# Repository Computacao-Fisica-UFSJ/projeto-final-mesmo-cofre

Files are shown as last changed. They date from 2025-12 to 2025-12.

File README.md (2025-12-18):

# 🐾 Projeto Yummy

- **Autores:** Ester Maria e Mateus Brito
- **Baseado em:** [Automatic Arduino Powered Pet Feeder](https://www.instructables.com/Automatic-Arduino-Powered-Pet-Feeder/)
- **Data:** 2025-12-17

---

## Sumário
- [Contextualização](#contextualização)
- [Guia do Usuário](#guia-do-usuario)
- [Código e Bibliotecas](#código-e-bibliotecas)
- [Lista de Materiais](#lista-de-materiais)
- [Diagrama da Montagem (Fritzing)](#diagrama-da-montagem-fritzing)
- [Explicação do Diagrama](#explicação-do-diagrama)
- [Foto do Projeto Montado](#foto-do-projeto-montado)
- [Vídeo do Projeto em Funcionamento](#vídeo-do-projeto-em-funcionamento)
- [Problemas Encontrados](#problemas-encontrados)
- [Evolução do Projeto](#evolução-do-projeto)
- [Referências](#referências)
- [Créditos](#créditos)

---

## Contextualização
O **Projeto Yummy** consiste no desenvolvimento de um alimentador automático de pets, utilizando a plataforma Arduino, com foco em automação, controle de quantidade de ração e interação do usuário via interface web.

A motivação do projeto surge da necessidade de garantir que animais de estimação recebam a quantidade correta de alimento, mesmo na ausência do dono, evitando tanto a subalimentação quanto o excesso de ração. Para isso, o sistema combina atuadores mecânicos, sensor de peso (balança) e conectividade Wi-Fi, permitindo um controle mais preciso e automatizado do processo.

Diferentemente de alimentadores baseados apenas em tempo, o Yummy utiliza uma balança calibrada para medir a quantidade real de ração servida. Dessa forma, o processo de liberação só é finalizado quando o peso configurado pelo usuário é atingido, aumentando a confiabilidade do sistema.

---

## Guia do Usuário
Essa seção descreve como o usuário interage com o alimentador automático por meio do navegador.

### Inicialização do Sistema
- Conecte o Arduíno à fonte de alimentação.
- Aguarde alguns segundos para que o módulo Wi-fi inicializa corretamente.

### Acesso à Interface Web
- O dispositivo deve estar conectado à mesma rede configurada no código .ino (por padrão, o código está conectado à rede da UFSJ).
- Abra um navegador de internet
- Digite o endereço "172.18.191.210" na barra de navegação.
- Ao acessar o endereço, a página de controle do alimentador será exibida.

### Configuração da Quantidade de Ração
- Na interface web, o usuário pode configurar a quantidade de ração desejada, em quilogramas.
- O valor padrão configurado no sistema é 0.06 kg.

### Servir a Ração
- Após definida a quantidade desejada, pressione o botão "Iniciar" na interface.
- O servo agitador começa a movimentar a reção no reservatório.
- Em seguida, o motor responsável pela liberação da ração é acionado.
- A ração é liberada gradualmente.
- A balança monitora o peso em tempo real.
- O sistema interrompe automaticamente a liberação quando o peso configurado é atingido.

### Finalização do Processo
- Ao atingir o peso desejado os motores são desligados e o processo de alimentação é encerrado.
- O sistema fica pronto para uma nova configuração ou novo acionamento.

---

## Códigos e Bibliotecas

### Código principal utilizado
Arquivo principal: 'codigo.ino'

### Bibliotecas (não-padrão)
- **HX711** (`HX711.h`) — *Bogdan Necula*  
  - Via Library Manager: buscar por `HX711`  

- **Servo** — geralmente já disponível na IDE do Arduino (padrão).

### Observações sobre compilação
- Plataforma alvo: **Arduino Uno**
- Antes de compilar, verifique se a biblioteca `HX711` está instalada; caso contrário, instale via **Sketch → Include Library → Manage Libraries**.

---

## Materiais

### 🔌 Componentes 
- **1x** Servo motor (utilizado no projeto: SG90)
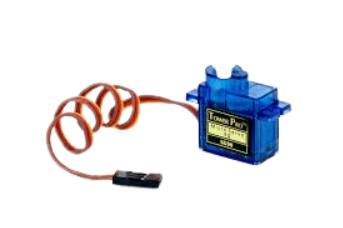
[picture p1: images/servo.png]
Servo Motor
  
- **1x** Micro Motor DC N20 
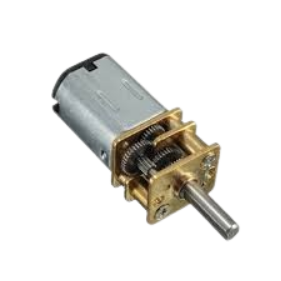
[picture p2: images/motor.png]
Micro Motor
  
- **1x** Peça impressa em 3D para movimentação da ração
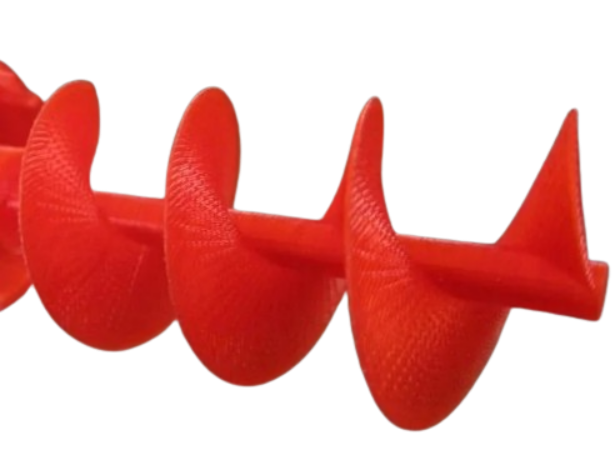
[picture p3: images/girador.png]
Rosca

- **1x** Peça impressa em 3D para agitar a ração
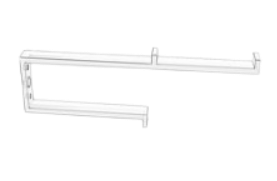
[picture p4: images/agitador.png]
Agitador

- **1x** Tubo de PVC em T de **1 ½"**  
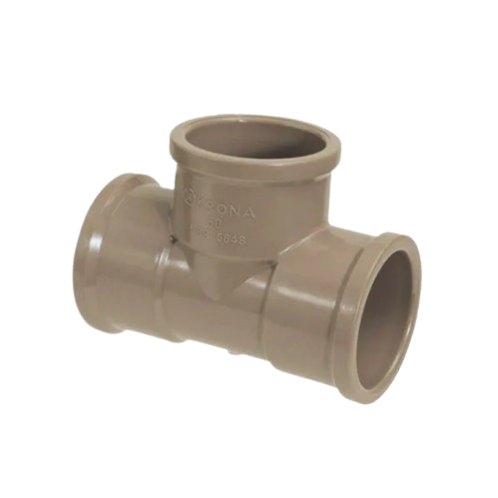
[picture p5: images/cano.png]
Tubo PVC

- **1x** Arduino Mega  
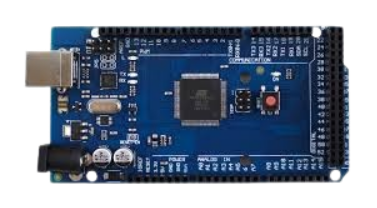
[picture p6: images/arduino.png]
Arduíno Mega

- **1x** Módulo Wi-Fi ESP8266
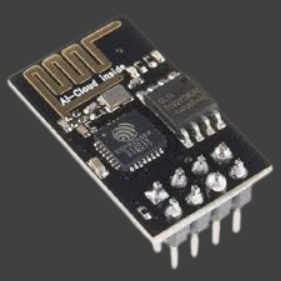
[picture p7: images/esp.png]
Módulo Wi-fi

- **1x** Placa HX711
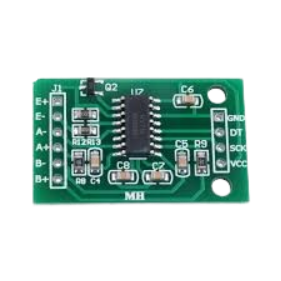
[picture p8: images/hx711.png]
HX711

- **1x** Módulo Ponte H
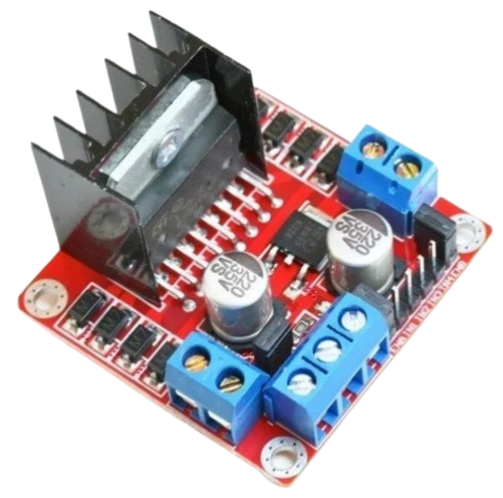
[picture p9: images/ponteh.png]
Ponte H

- **1x** Reservatório de ração 
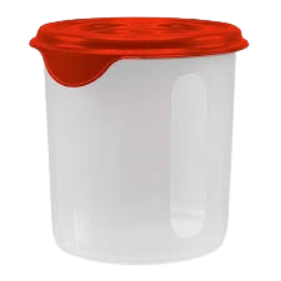
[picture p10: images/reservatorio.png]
Reservatório

- **1x** Caixa de montagem  
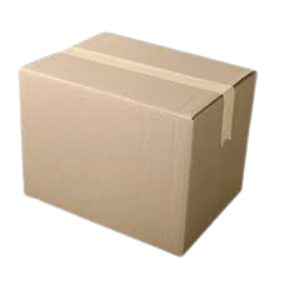
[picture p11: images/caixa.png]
Caixa

- **1x** Balança (Seu sensor de peso foi utilizado)
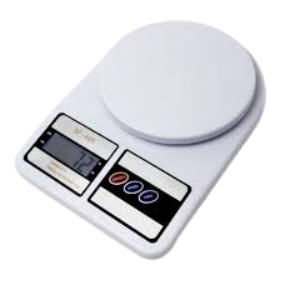
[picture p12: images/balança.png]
Balança

- **1x** Impressora 3D  

---

## Diagrama da Montagem (Fritzing)

- Arquivo Fritzing do projeto: `fritzing/fritzing.fzz`  
- Os componentes que foram importados separadamente se encontram na pasta "fritzing".

---

## Explicação do Diagrama

1. **Arduíno Mega**  
   - **Função**: unidade central de controle do projeto. É responsável por processar os dados da balança, receber comandos da interface web e controlar os motores.
   - **Conexões**: 
      - Alimentação via USB

2. **Servo motor (Agitador de ração)**  
   - **Função**: movimenta a ração dentro do reservatório, evitando que ela fique presa antes de ser liberada.
   - **Conexões**: 
      - Sinal: pino digital
      - VCC: 5V
      - GND: GND

3. **Motor DC (Liberação da ração)**  
   - **Função**: aciona o mecanismo responsável por liberar a ração pelo tubo de PVC.
   - **Conexões**: 
      - Terminais do motor conectados à ponte H

4. **Célula de Carga (Balança)**  
   - **Função**: mede o peso da ração liberada, permitindo que o sistema interrompa o processo ao atingir o valor configurado.
   - **Conexões**: 
      - Fios da célula conectados ao módulo HX711 (E+, E−, A+, A−)

5. **Módulo HX711**  
   - **Função**: amplifica e converte o sinal analógico da célula de carga em dados digitais compreensíveis pelo Arduino.
   - **Conexões**: 
      - DT (Data): pino digital do Arduino
      - SCK: pino digital do arduíno
      - VCC: 5V
      - GND: GND
      - Entradas conectadas à célula de carga

6. **Módulo Wi-Fi (ESP8266)**  
   - **Função**: permite a comunicação do Arduino com a rede Wi-Fi, possibilitando o controle do alimentador via navegador.
   - **Conexões**: 
      - TX: RX do arduíno
      - RX: TX do arduíno
      - VCC: 5V
      - GND: GND

7. **Fonte de Alimentação Externa**  
   - **Função**: fornece energia suficiente para os motores e servos, evitando sobrecarga no Arduino.

---

## Foto do Projeto Montado

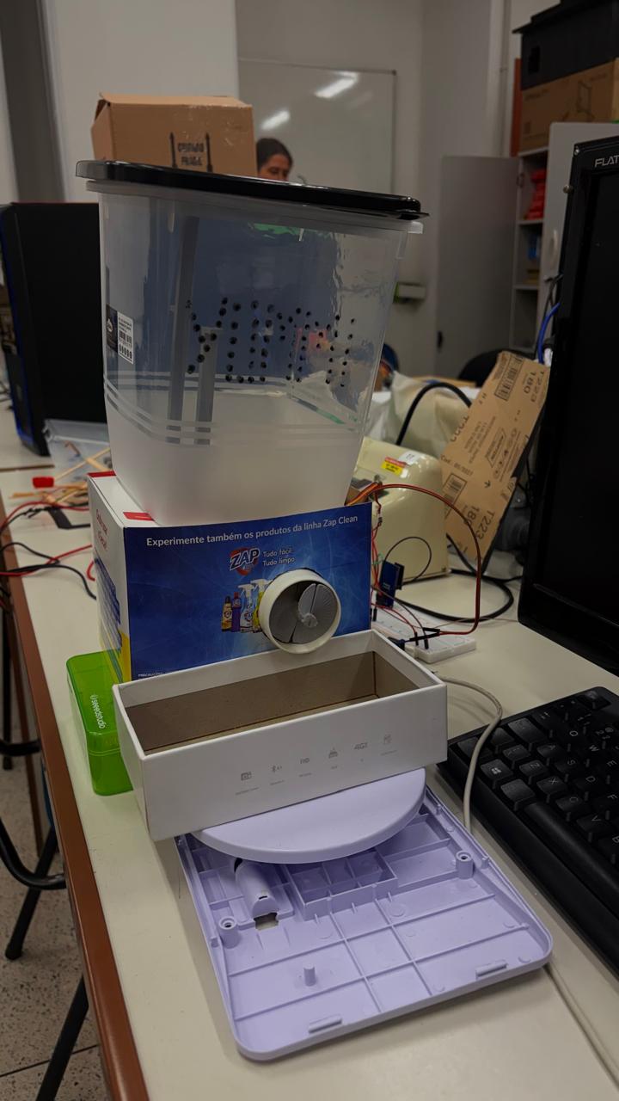
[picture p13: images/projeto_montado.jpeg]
Foto do projeto montado


---

## Vídeo do Projeto em Funcionamento
 
Link direto do vídeo: `https://drive.google.com/file/d/1mnle7g3bbe9a2HnBpE-G1RTfhmxTSZ-H/view?usp=sharing`

---

## Problemas Encontrados no Processo de Montagem

- **Encaixe da rosca no cano PVC:** dificuldade ao fazer o encaixe perfeito da rosca no cano PVC. A conexão da rosca impressa 3d com o motor, e seu encaixe dentro do cano não funcionou bem, ela não rodava sempre com perfeição. Além disso, a fixação do motor foi uma tarefa difícil.
- **Alimentação:** devido à quantidade de componentes do projeto, somente a alimentação do arduíno não foi suficiente.
- **Balança:** realizar a abertura da balança, a calibração da célula de carga e conexão dos fios foi um pouco complicado.
- Em geral, enfrentamos mais dificuldades na parte física do projeto.

---

## Evolução do Projeto

### Etapas realizadas até a aula do dia 19/11:
- Abertura da balança: tentamos entender como a informação é passada pelos componentes da balança e vimos que seria necessário o uso de um módulo conversor para o sensor de peso (HX711).
- Solda dos fios que saem do sensor de peso da balança na placa HX711, e dos fios que saem da mesma placa para serem enviados para a placa Arduíno.
- Com a conexão do sensor de peso ao arduíno, realizamos a calibração da balança com um código.
- Conexão do servo ao projeto: esse servo controlará o agitador de ração. Produzimos um código inicial, o qual aguarda o sinal de botão para agitar a ração, até que um certo peso na balança é atingido. 

### Aula 25/11:
- Análise de motores possíveis para controlar a rosca que libera a ração. Escolhemos o Micro Motor DC N20 e tentamos conectá-lo à uma ponte H para dividir a alimentação. Contudo, tivemos problema com a fonte que utilizamos e resolvemos conectar o motor diretamente ao arduíno. Incluímos essa parte no código, ativando o motor depois que o servo do agitador para, até que o peso seja atingido.

### Aula 26/11:
- Iniciamos a lógica do Wi-Fi, entendendo o funcionamento do módulo ESP8266. Utilizamos um código teste para testarmos o módulo.

### Aula 03/12:
- Unimos o código da lógica do projeto com o código teste do Wi-Fi. Criamos funções com lógica de máquina de estado para o funcionamento do projeto. Começamos o html para o cliente realizar as requisições pela web. Em geral, está funcionando bem. Alguns problemas surgiram no meio do caminho e precisam ser solucionados.

### Aula 09/12:
- Começamos a montar a parte estrutural do projeto. Conectar os componentes, parafusar itens, etc.

### Aula 10/12:
- Tivemos problema com a peça que serve a ração e sua conexão com o motor. O motor não estava estruturalmente estável, o que fazia com que a peça travasse dentro do cano PVC. Passamos o dia tentando solucionar este problema.

### "Aula" 15/12:
- Com o problema da peça que serve a ração inicialmente solucionado, resolvemos problemas com o código, como html para requisição e configuração da tara da balança. Além disso, fizemos as atualizações necessárias no Fritizing do projeto. Ao iniciarmos a montagem do projeto, vimos que a energia fornecida pelo arduíno não seria suficiente, tendo em vista que o motor não estava funcionando. Com isso, foi necessário utilizar fontes de energia externas, como point H.

### "Aula" 15/12:
- Com os problemas estruturais e de software resolvidos, partimos para a montagem final do projeto.
---

## Referências

- Automatic Arduino Powered Pet Feeder: https://www.instructables.com/Automatic-Arduino-Powered-Pet-Feeder/

---

## Créditos

- Arthur Carvalho: ajuda na implementação do Wi-Fi
- Davi Greco: ajuda na solda de alguns componentes
- Milene: ajuda no mental e na parte estrutural

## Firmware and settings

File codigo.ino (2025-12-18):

// INCLUSÃO DE BIBLIOTECAS
#include <HX711.h>
#include <Servo.h>

// DEFINIÇÕES DE PINOS
#define pinDT  2
#define pinSCK  3
#define pinMotor1 8
#define pinMotor2 9
#define DEBUG true

int estado = 0;
int pos = 0;
float pesoDesejado = 0.06;

// INSTANCIANDO OBJETOS
HX711 scale;

// DECLARAÇÃO DE VARIÁVEIS
float medida = 0;
Servo agitadorServo;

void setup() {
  Serial.begin(57600);
  Serial1.begin(115200); // Comunicação com ESP8266 (baud rate padrão AT)

  // Reseta o módulo
  sendData("AT+RST\r\n", 2000, DEBUG);
  delay(3000);
  // Conecta ao WiFi
  sendData("AT+CWJAP=\"WIFI_UFSJ\",\"\"\r\n", 2000, DEBUG);
  delay(5000);
  // Configura como Station
  sendData("AT+CWMODE=1\r\n", 1000, DEBUG);
  // Mostra IP atribuído
  sendData("AT+CIFSR\r\n", 1000, DEBUG);
  // Habilita múltiplas conexões
  sendData("AT+CIPMUX=1\r\n", 1000, DEBUG);
  // Inicia servidor na porta 80
  sendData("AT+CIPSERVER=1,80\r\n", 1000, DEBUG);
  
  pinMode(pinMotor1, OUTPUT);
  pinMode(pinMotor2, OUTPUT);
  scale.begin(pinDT, pinSCK); // CONFIGURANDO OS PINOS DA BALANÇA
  scale.set_scale(434341); // LIMPANDO O VALOR DA ESCALA

  delay(2000);
  scale.tare(); // ZERANDO A BALANÇA PARA DESCONSIDERAR A MASSA DA ESTRUTURA

  Serial.println("Balança Zerada");

  estado = 0;
}

void loop() {
  scale.power_down();
    
  if(Serial1.available()){
    if(Serial1.find("+IPD,")){ // "+IPD" indica que chegou uma requisição HTTP
      delay(300);
      //int connectionId = Serial1.read() - 48; // Pega o ID da conexão (char -> int)
      int connectionId = Serial1.read() - '0';
      
      // Limpa o buffer até encontrar os dados da requisição
      while(Serial1.available() && Serial1.read() != ':') {}

      // Lê a linha da requisição HTTP
      String request = Serial1.readStringUntil('\r');
      Serial.println("Requisicao: " + request);

      if (request.indexOf("GET /start") >= 0) {
          Serial.println("Botão pressionado via WiFi!");
          estado = 1;
      }

      // ----------- SETAR PESO VIA HTML -----------
      if (request.startsWith("GET /setpeso")) {
      
        int idx = request.indexOf("valor=");
        if (idx > 0) {
      
          int endIdx = request.indexOf(' ', idx);
          if (endIdx < 0) endIdx = request.length();
      
          String valorStr = request.substring(idx + 6, endIdx);
      
          pesoDesejado = valorStr.toFloat();
      
          Serial.print("Peso desejado atualizado para: ");
          Serial.println(pesoDesejado, 3);
        }
      }
      
      // ------------------ RESPOSTA HTML ------------------
      String response = "HTTP/1.1 200 OK\r\n";
      response += "Content-Type: text/html\r\n";
      response += "Connection: close\r\n\r\n";
      
      response += "<!DOCTYPE html><html lang='pt-BR'>";
      response += "<head>";
      response += "<meta charset='UTF-8'>";
      response += "<meta name='viewport' content='width=device-width, initial-scale=1.0'>";
      
      response += "<style>";
      response += "body{"
                  "margin:0;"
                  "font-family: 'Segoe UI', Arial, sans-serif;"
                  "background: linear-gradient(135deg, #f5f7fa, #c3cfe2);"
                  "display:flex;"
                  "justify-content:center;"
                  "align-items:center;"
                  "height:100vh;"
                  "}";
      response += ".card{"
                  "background:#fff;"
                  "padding:30px;"
                  "border-radius:15px;"
                  "box-shadow:0 10px 30px rgba(0,0,0,0.15);"
                  "max-width:400px;"
                  "width:100%;"
                  "text-align:center;"
                  "}";
      response += "h1{"
                  "margin-bottom:10px;"
                  "color:#333;"
                  "}";
      response += "p{"
                  "font-size:18px;"
                  "color:#555;"
                  "}";
      response += "input[type=number]{"
                  "width:100%;"
                  "padding:12px;"
                  "font-size:20px;"
                  "margin-top:10px;"
                  "border-radius:8px;"
                  "border:1px solid #ccc;"
                  "}";
      response += "input[type=submit]{"
                  "width:100%;"
                  "margin-top:15px;"
                  "padding:15px;"
                  "font-size:20px;"
                  "background:#4CAF50;"
                  "color:white;"
                  "border:none;"
                  "border-radius:10px;"
                  "cursor:pointer;"
                  "}";
      response += "input[type=submit]:hover{background:#45a049;}";
      response += "button{"
                  "width:100%;"
                  "margin-top:25px;"
                  "padding:20px;"
                  "font-size:26px;"
                  "background:#2196F3;"
                  "color:white;"
                  "border:none;"
                  "border-radius:12px;"
                  "cursor:pointer;"
                  "}";
      response += "button:hover{background:#1e88e5;}";
      response += "</style>";
      
      response += "</head><body>";
      
      response += "<div class='card'>";
      response += "<h1>🐾 Yummi! Alimentador</h1>";
      
      response += "<p>Peso desejado atual:</p>";
      response += "<p><b>";
      response += String(pesoDesejado, 3);
      response += " kg</b></p>";
      
      response += "<form action='/setpeso' method='GET'>";
      response += "<label>Definir peso (kg)</label>";
      response += "<input type='number' step='0.01' name='valor' required>";
      response += "<input type='submit' value='Salvar Peso'>";
      response += "</form>";
      
      response += "<button onclick=\"location.href='/start'\">Iniciar Alimentação</button>";
      
      response += "</div>";
      
      response += "</body></html>";

      // Envia página ao cliente via ESP8266
      String cipSend = "AT+CIPSEND=" + String(connectionId) + "," + String(response.length()) + "\r\n";
      sendData(cipSend, 1000, DEBUG);
      sendData(response, 1000, DEBUG);

      // Fecha a conexão
      sendData("AT+CIPCLOSE=" + String(connectionId) + "\r\n", 3000, DEBUG);
    }
  }

  if(estado == 1){
     Serial.println("Começou!");
     agitarRacao();
     estado = 2;
  }

  
  if(estado == 2){
    servirRacao();
  }
  
}

void agitarRacao(){
  // Stir servo section    
   agitadorServo.attach(4);    
   for(pos = 0; pos <= 180; pos += 1) {                                  
    agitadorServo.write(pos);              
    delay(5);   
   } 
   for(pos = 180; pos>=0; pos-=1)  {                                
    agitadorServo.write(pos);          
    delay(10);   
   } 
   delay(200);
   for(pos = 0; pos <= 180; pos += 1) {                                  
    agitadorServo.write(pos);              
    delay(10);
   } 
   for(pos = 180; pos>=0; pos-=1)  {                                
    agitadorServo.write(pos);          
    delay(5);
   }  
   agitadorServo.detach();  
}

void servirRacao(){
  Serial.println("Entrei!");
  scale.power_up();
  medida = scale.get_units(5); // SALVANDO NA VARIAVEL O VALOR DA MÉDIA DE 5 MEDIDAS
  Serial.println(medida, 3); // ENVIANDO PARA MONITOR SERIAL A MEDIDA COM 3 CASAS DECIMAIS

  digitalWrite(pinMotor1, HIGH);
  digitalWrite(pinMotor2, LOW);
  
  scale.power_down(); // DESLIGANDO O SENSOR
  delay(1000); // AGUARDA 5 SEGUNDOS
  scale.power_up(); // LIGANDO O SENSOR  

  if(medida >= pesoDesejado){
    digitalWrite(pinMotor1, LOW);
    digitalWrite(pinMotor2, LOW);
    estado = 0;
  }
}

// Função que envia comandos AT ao ESP8266 e retorna resposta
String sendData(String command, const int timeout, boolean debug){
  String response = "";
  Serial1.print(command);
  long int time = millis();
  while ((time + timeout) > millis()){
    while (Serial1.available()){
      char c = Serial1.read();
      response += c;
    }
  }
  if(debug){
    Serial.println(response); // Mostra resposta do ESP8266
  }
  return response;
}
